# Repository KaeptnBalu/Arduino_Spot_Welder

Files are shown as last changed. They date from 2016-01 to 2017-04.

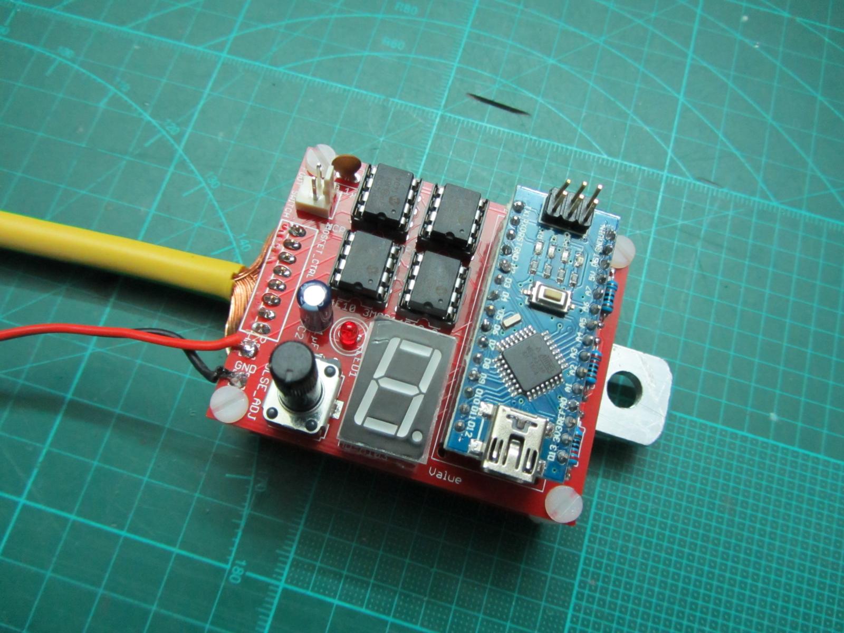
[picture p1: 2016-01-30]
Spot_Welder_Assembly_4.JPG

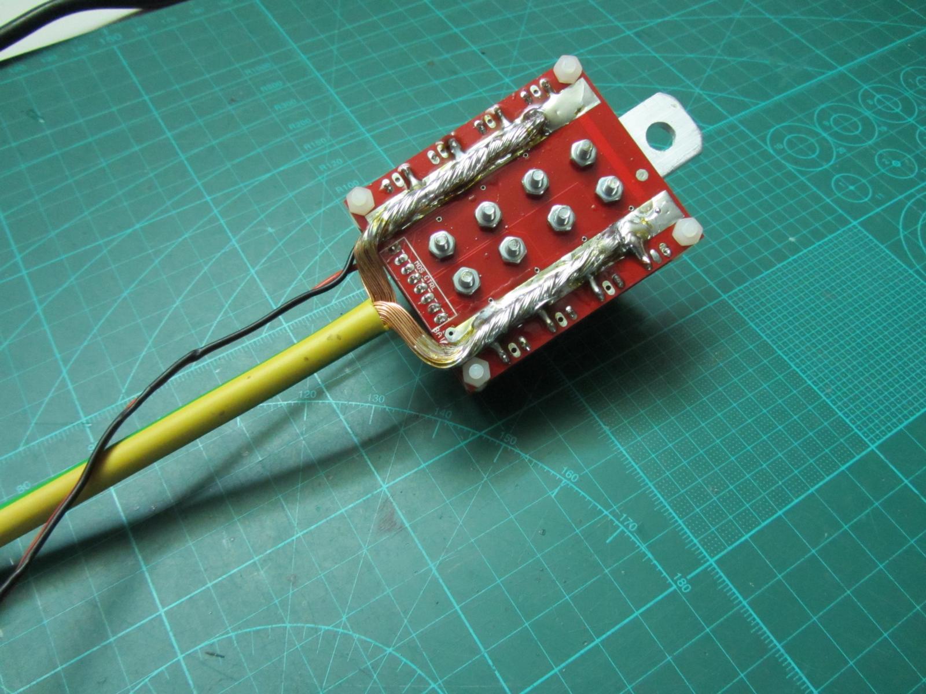
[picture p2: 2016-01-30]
Spot_Welder_Assembly_3.JPG

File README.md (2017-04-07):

# Arduino_Spot_Welder
There is a new Version of this project available: https://github.com/KaeptnBalu/Arduino_Spot_Welder_V2

An Arduino based Spot Welder for battery welding
http://www.instructables.com/id/DIY-Arduino-Battery-Spot-Welder/

This Spot Welder can be used to weld 18650 batteries. It needs a 7-12V power source (12V recommended) and uses a 12V car battery as welding current supply. Typically one 45Ah battery delivers enough current to get good welds with 0.15mm nickel strips. For thicker nickel strips maybe you will need bigger battery or two in paralell.

The Welder generates a double pulse, where the first one is 1/8 of the time of the second one. Pulse time of second pulse is adjustable by the potentiometer and displayed on the screen in mS so you can exactly adjust the time. Its adjustable from 1 ... 20 mS.

If you want to download the project click on "Download ZIP" on this page. Downloading single files sometimes seems to cause some files to be corrupted while downloading.

You can get parts to build your own Spot Welder or prebuilt kits at https://malectrics.eu/

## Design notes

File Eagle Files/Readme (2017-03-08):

The spot welder is made of two boards which are stacked on top of each other.
One board contains all the logic and low power electronic components and the other one contains the Mosfets.

---------------------------------------------------------------------------------------------------------

Update (01.2017): Spot_welder_gerber.zip is now accepted by pcb way without problems

---------------------------------------------------------------------------------------------------------

The gerber files are made to be used at pcbway.com 
You can support me by registering through this link http://www.pcbway.com/setinvite.aspx?inviteid=12824
This way you get a 5$ coupon for your order and i get some credits at the shop which i can use for upcoming projects.

There are two versions of the gerber files available.

1.
You can use the Spot_welder_gerber.zip which has both boards combined to one big board. 
You have to cut this in half at home to get the two single boards.

2.
You can use the Arduino_Board_Gerber.zip and the Mosfet_Board_Gerber.zip . So you have one gerber file for each board. 
This means you have to order both boards seperately which is more expensive, but no cutting at home is required.
(these are not the latest Version at the moment, i will update them in some weeks.)

To download Zip files click on them and then click "view raw". 
Downloading by right click and "save as" does seem to cause problems.

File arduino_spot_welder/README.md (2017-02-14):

The code for the Spot welder is the arduino_spot_welder.ino . Use this for normal operation.

If you built the spot welder yourself but it doesn't work, you can use the TEST_MODE_Arduino_Spot_Welder.ino to find the error.
DO NOT CONNECT THE WELDING WIRES WHEN USING THIS CODE !
With the test code pushing the foot switch turns the mosfets permanent on. This way you can measure all the voltages with a normal multimeter. 
For example you can check: 
- if all mosfet gates get the full voltage when they are on. They should have almost the voltage of your power supply.
- if the Arduino outputs a high signal (5V) to the mosfet drivers
- if the LED gets a high signal (5V)

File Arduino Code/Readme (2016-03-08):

// Simply copy and paste the code into a new sketch in your Arduino Software

int mosfetPin = 5;
int ledPin = 4;
int tasterPin = 2;
int sensorPin = 7;
int sensorValue = 0;
int pulse_time;
int pulse_short;
int pulse_long;

//            0           1          2          3          4          5          6          7          8          9          .
byte z[11]={B11111101, B01100001, B11011011, B11110011, B01100111, B10110111, B10111111, B11100001, B11111111, B11110111, B00000001};

//-------------------------------------------------------------------------------------------

void setup() {

pinMode(tasterPin,INPUT);  // set tasterPin as Input
pinMode(mosfetPin,OUTPUT);  // set mosfetPin as Output
pinMode(ledPin,OUTPUT);  // set ledPin as Output

// 7 Segment Pins
for (int i=6; i <= 13; i++) // 6-13 are set as Outputs
    pinMode(i,OUTPUT);

}

//-------------------------------------------------------------------------------------------

void loop() {

time_display();

// impuls activated by taster
if (digitalRead(tasterPin)==HIGH){
    DoppelImpuls();
    do {
  digitalWrite(mosfetPin, LOW);
  digitalWrite(ledPin, LOW);
} while (digitalRead(tasterPin)==HIGH);
  delay(500);
                                  } 
else 
{
    digitalWrite(mosfetPin, LOW);
    digitalWrite(ledPin, LOW);
}

}

//-------------------------------------------------------------------------------------------

void segmente(byte n) {
// controll all 7 Segments
 
  for(int k=6; k <= 13; k++) {
    if((n & B10000000) > 0)
      digitalWrite(k, HIGH);
    else 
      digitalWrite(k, LOW);
    n = n << 1;
  } 
  }

//-------------------------------------------------------------------------------------------  

void time_display(){  // 7 segment pulse time displaying
  
pulse_time = analogRead(sensorPin)/51.15;

int b=(pulse_time%100)/10;		//Zehner
int a=pulse_time%10;                //Einer

if (b==0)
{
segmente(z[10]);
    delay(100);
}
else
{
segmente(z[b]);
    delay(400);
}    
segmente(z[a]);
    delay(400);
segmente(z[10]);
    delay(700);    
  }

//-------------------------------------------------------------------------------------------

void DoppelImpuls(){  
  sensorValue = analogRead(sensorPin);
 
  pulse_long  = (sensorValue/51.15);   //makes a pulse of max 20 mS because SensorValue can max become 1023
  pulse_short = (pulse_long/8);     // Impuls with 1/8 of the time of pulse_long
 
  if (pulse_short < 1)
     pulse_short = 1; 
 
  digitalWrite(ledPin, HIGH);
  digitalWrite(mosfetPin, HIGH);
  delay(pulse_short);
  digitalWrite(mosfetPin, LOW);
  delay(pulse_short);      
    digitalWrite(mosfetPin, HIGH);
  delay(pulse_long);   
  digitalWrite(mosfetPin, LOW);
  delay(sensorValue);
  digitalWrite(ledPin, LOW);
  
}

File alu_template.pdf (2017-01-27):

17,00 mm

70,00 mm

# Cut from 3 - 4 mm thick aluminum

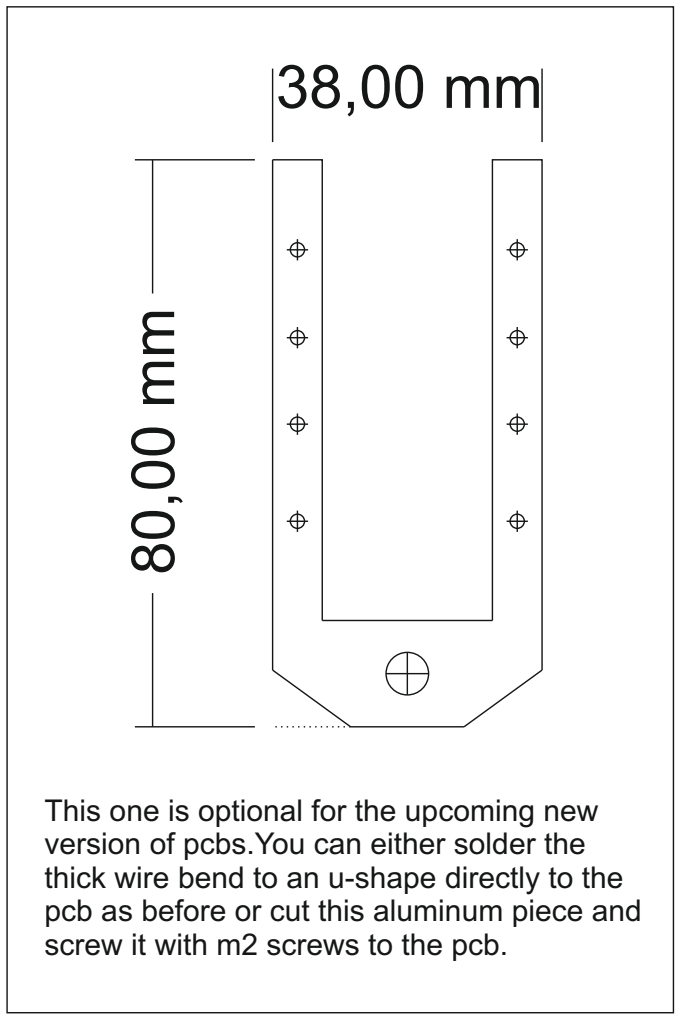
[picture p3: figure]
screw it with m2 screws to the pcb.

This one is optional for the upcoming new version of pcbs.You can either solder the thick wire bend to an u-shape directly to the pcb as before or cut this aluminum piece and

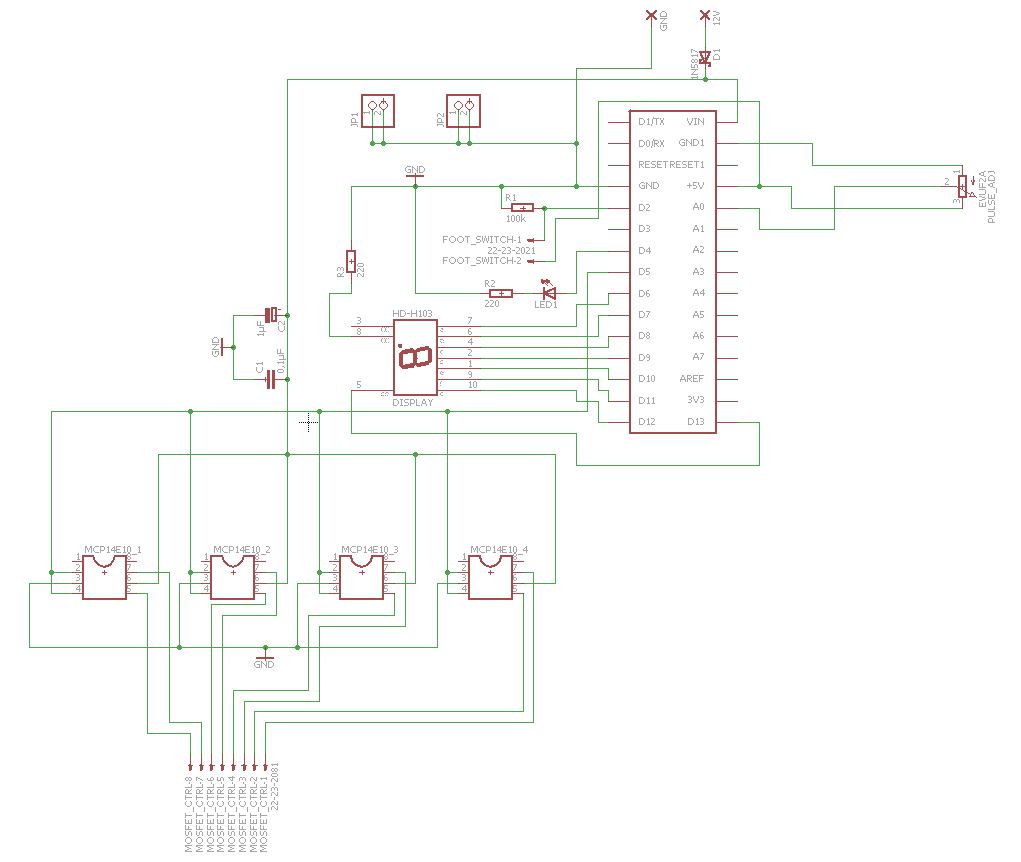
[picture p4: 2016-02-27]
Eagle Files/Arduino_pcb_schematic.JPG

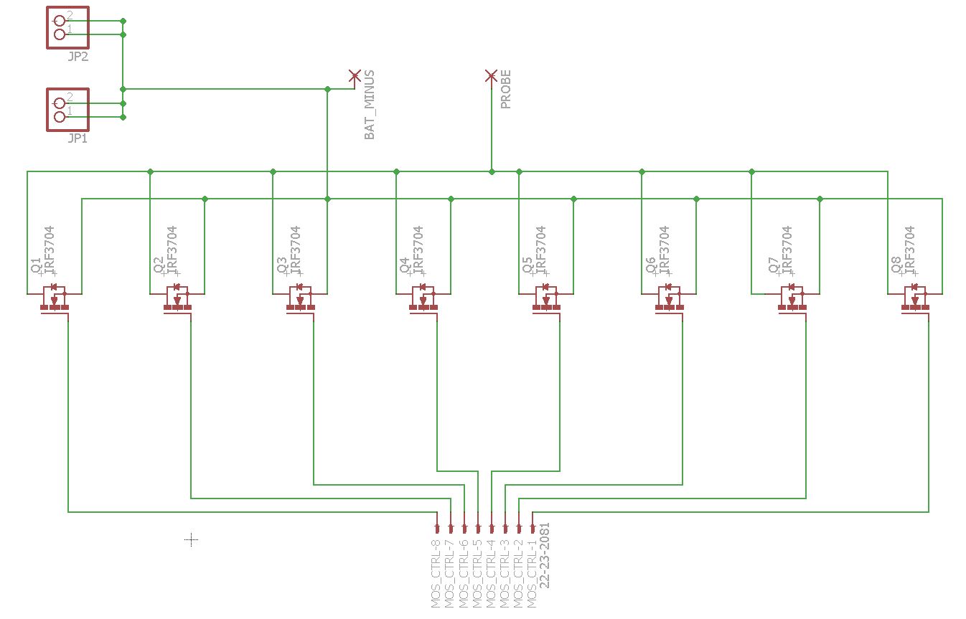
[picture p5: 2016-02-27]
Eagle Files/Mosfet.PCB_schematic.JPG

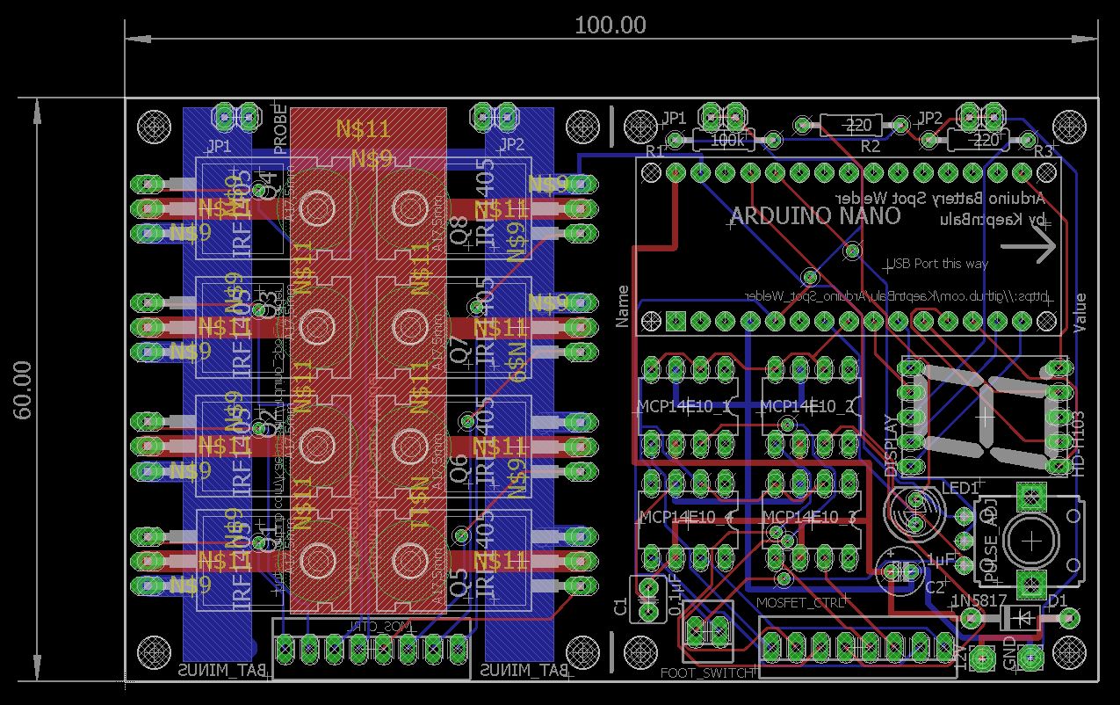
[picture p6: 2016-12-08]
Eagle Files/Gerber_combined_Boards.JPG

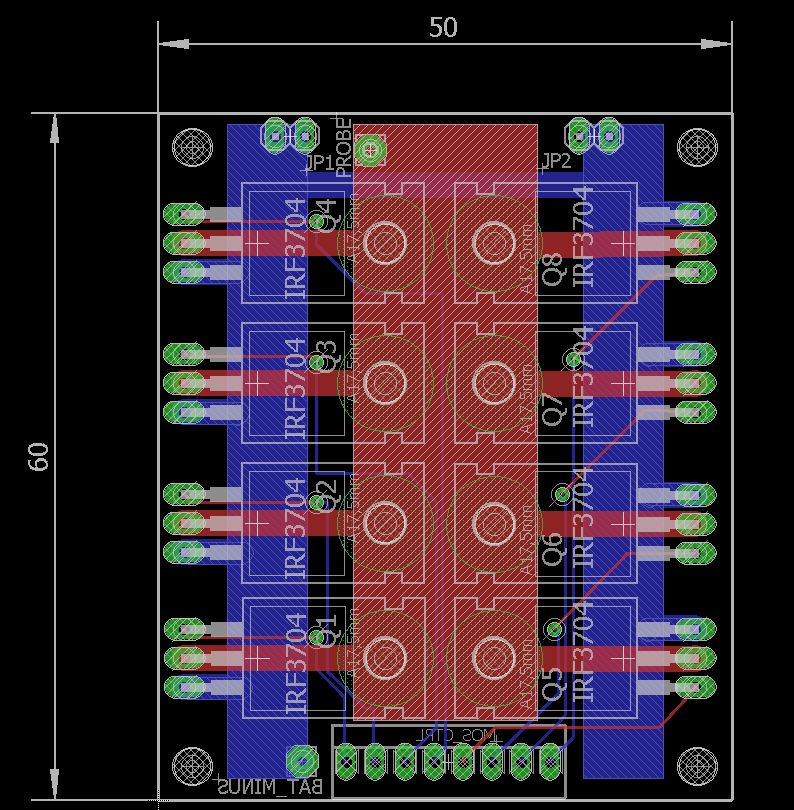
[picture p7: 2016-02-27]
Eagle Files/Mosfet.PCB_board.JPG

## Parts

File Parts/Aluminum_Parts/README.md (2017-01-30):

Use the PDF template to cut the aluminum pieces from 3-4mm material.

The u-shaped piece is optional.
You can either solder the thick wire bend to an u-shape directly to the  pcb as before 
or cut this aluminum piece and screw it with m2 screws to the pcb.
I have not tested the u-shaped alu piece yet because it is quite difficult to manufacture it with hand tools.

You can also take a look at the 3d and dxf drawings to manufacture the aluminum parts with a cnc or something else.

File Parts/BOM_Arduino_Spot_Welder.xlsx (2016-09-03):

 |  | Reichelt.de Parts |  |  | Complete Shopping Card Link (https://secure.reichelt.de/index.html?&ACTION=20&AWKID=1168721&PROVID=2084)
Quantity | Name | Reichelt.de Part Number | Price/piece | Price all | Reichelt.de Link
8 | Mosfet IRF1405 55V 169A | IRF 1405 | 1.15 € | 9.20 € | https://www.reichelt.de/IRC-IRF-Transistoren/IRF-1405/3/index.html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
4 | Mosfet Driver MCP14E10-E/P | MCP 14E10-E/P | 1.70 € | 6.80 € | https://www.reichelt.de/ICs-MCP-1-2-/MCP-14E10-E-P/3/index.html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
1 | Poti 6mm Linear 50K | RK09K113-LIN50K |  | 0.99 € | https://www.reichelt.de/6mm-Potis-mono/RK09K113-LIN50K/3/index.html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
1 | 7 Segment Display | SC 56-11 RT |  | 0.84 € | https://www.reichelt.de/Siebensegment-Anzeigen/SC-56-11-RT/3/index.html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
3 | 1x20pol female header | BL 1X20G8 2,54 | 0.26 € | 0.78 € | https://www.reichelt.de/Buchsenleisten/BL-1X20G8-2-54/3/index.html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
1 | 1x36pol male header | SL 1X36G 2,54 |  | 0.17 € | https://www.reichelt.de/Stiftleisten/SL-1X36G-2-54/3/index.html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
1 | PCB connector set 2pin | PS 25/2G WS |  | 0.29 € | https://www.reichelt.de/Platinen-Steckverbinder/PS-25-2G-WS/3/index.html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
4 | IC socket 8 pole | GS 8 | 0.03 € | 0.12 € | https://www.reichelt.de/IC-Sockel/GS-8/3/index.html?ACTION=3&GROUPID=3215&ARTICLE=8230&START=0&OFFSET=1000
1 | diode 1N5817 | 1N 5817 |  | 0.06 € | https://www.reichelt.de/1N-UF-AA-Dioden/1N-5817/3/index.html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
1 | elektrolytic capacitor 1 µF | RAD 1/63 |  | 0.04 € | https://www.reichelt.de/Elkos-radial-85-C/RAD-1-63/3/index.html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
1 | ceramic capacitor 100pF | KERKO 100P |  | 0.06 € | https://www.reichelt.de/Scheiben/KERKO-100P/3/index.html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
2 | Resistor 221 Ohm | METALL 221 | 0.08 € | 0.16 € | https://www.reichelt.de/1-4W-1-100-Ohm-976-Ohm/METALL-221/3/index.html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
1 | Resistor 100K-Ohm | METALL 100K |  | 0.08 € | https://www.reichelt.de/1-4W-1-100-k-Ohm-976-k-Ohm/METALL-100K/3/index.html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
1 | LED 5mm green | LED 5MM GN |  | 0.06 € | https://www.reichelt.de/LEDs-5-mm/LED-5MM-GN/3/index.html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
 |  | Other Parts
1 | Arduino Nano |  |  | 1.70 € | Aliexpress.com
1 | Aluminium 16x70x5mm |  |  | 2 € | local hardware Store
1 | 2m thick cable 16 or 25 mm² |  |  | 0 € | e.g. old car starter cable
1 | 0,5m 10mm² solid copper wire | for the welding tips |  | 1 € | local hardware store
3 | cable lug for 16 - 25mm² |  | 0.6 | 1.80 € | local hardware store or http://www.voelkner.de/products/9287/Ringkabelschuh-16-25mm-6mm-Gelb.html
1 | battery clip | for car battery |  | 1.95 € | local hardware store or http://www.voelkner.de/products/80594/Batterieklemme-Gerade-Plus-Minus.html
1 | PCB | from pcb manufacturer |  | 20.00 € | pcbway.com (you get 10 pcbs for this price)
 |  | TOTAL PARTS COST |  | 48.10 €

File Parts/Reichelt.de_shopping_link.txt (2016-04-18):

https://secure.reichelt.de/index.html?&ACTION=20&AWKID=1203408&PROVID=2084

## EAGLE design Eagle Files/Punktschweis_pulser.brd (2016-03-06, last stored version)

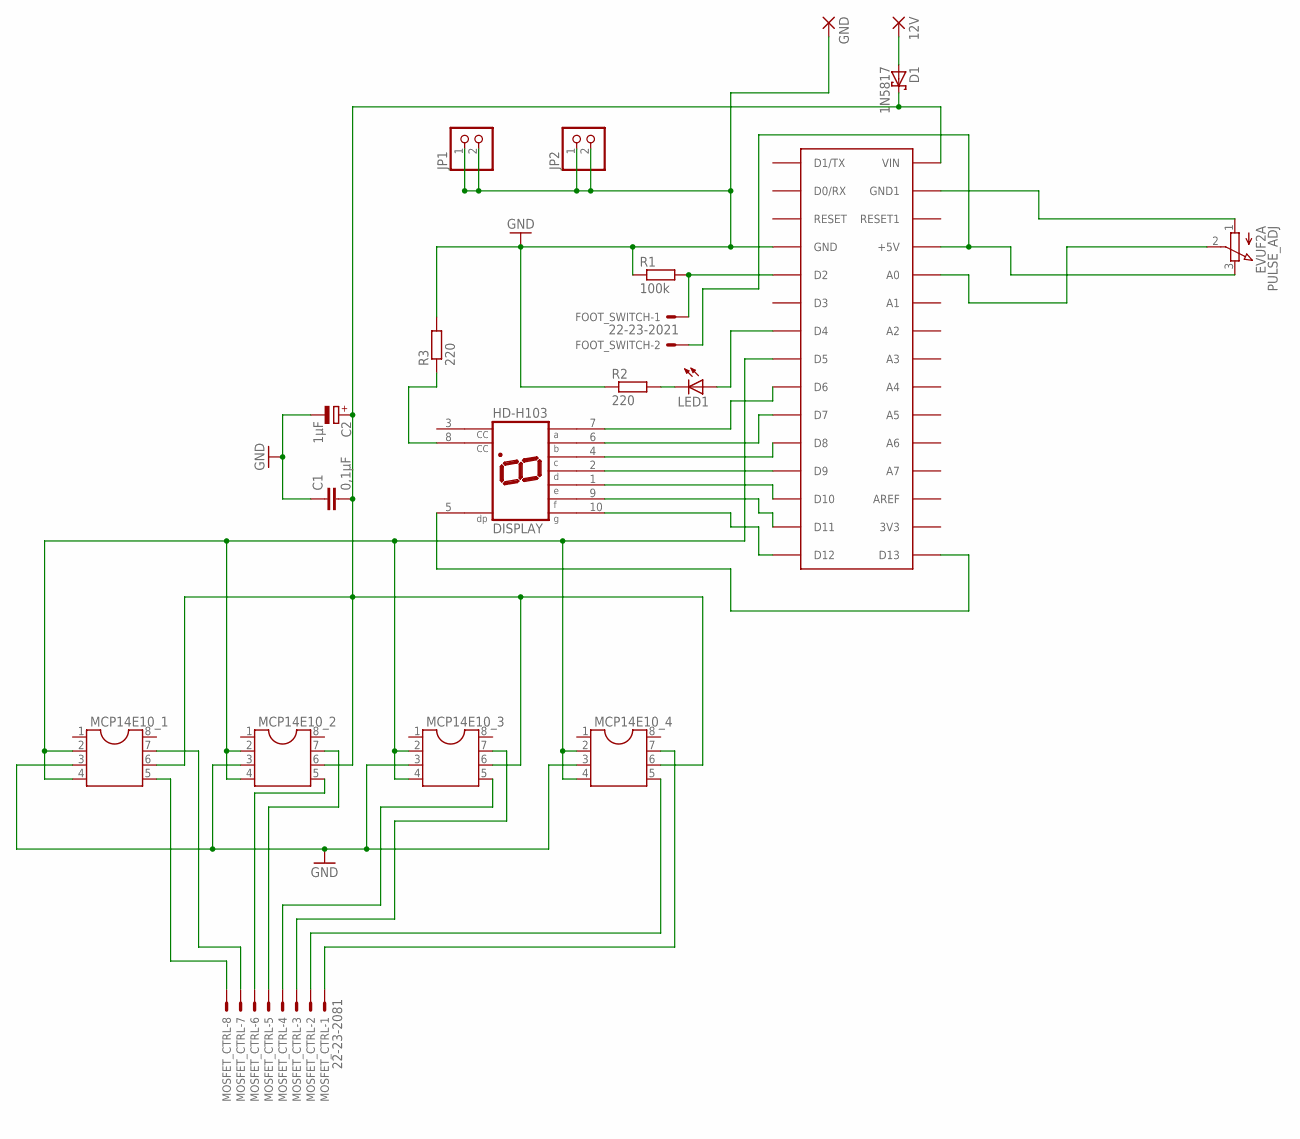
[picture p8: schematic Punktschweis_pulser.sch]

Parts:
12V: 2,54/0,8
C1: 0,1µF; C2.5-4
C2: 1µF; E2-5
D1: 1N5817; DO41-10
DISPLAY: HD-H103; HDSP-M
FOOT_SWITCH: 22-23-2021
GND: 2,54/0,8
JP1, JP2: PINHD-1X2; 1X02
LED1: LED5MM
MCP14E10_1, MCP14E10_2, MCP14E10_3, MCP14E10_4: DIL8; DIL08
MOSFET_CTRL: 22-23-2081
PULSE_ADJ: EVUF2A; EVUF
R1: 100k; 0207/10
R2, R3: 220; 0207/10
U$1: ARDUINONANO; PDIP-32

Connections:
GND: C1.1, C2.-, GND.1, JP1.1, JP1.2, JP2.1, JP2.2, MCP14E10_1.3, MCP14E10_2.3, MCP14E10_3.3, MCP14E10_4.3, R1.1, R2.1, R3.2, U$1.GND
unnamed: DISPLAY.7 (A), U$1.D6
unnamed: MCP14E10_1.5, MOSFET_CTRL.8
unnamed: C1.2, C2.+, D1.C, MCP14E10_1.6, MCP14E10_2.6, MCP14E10_3.6, MCP14E10_4.6, U$1.VIN
unnamed: PULSE_ADJ.1 (A), U$1.GND1
unnamed: FOOT_SWITCH.2, PULSE_ADJ.3 (E), U$1.+5V
unnamed: PULSE_ADJ.2 (S), U$1.A0
unnamed: FOOT_SWITCH.1, R1.2, U$1.D2
unnamed: LED1.K (C), R2.2
unnamed: LED1.A, U$1.D4
unnamed: MCP14E10_1.7, MOSFET_CTRL.7
unnamed: MCP14E10_2.5, MOSFET_CTRL.6
unnamed: MCP14E10_2.7, MOSFET_CTRL.5
unnamed: DISPLAY.6 (B), U$1.D7
unnamed: MCP14E10_3.5, MOSFET_CTRL.4
unnamed: MCP14E10_3.7, MOSFET_CTRL.3
unnamed: MCP14E10_4.5, MOSFET_CTRL.2
unnamed: MCP14E10_4.7, MOSFET_CTRL.1
unnamed: DISPLAY.4 (C), U$1.D8
unnamed: MCP14E10_1.2, MCP14E10_1.4, MCP14E10_2.2, MCP14E10_2.4, MCP14E10_3.2, MCP14E10_3.4, MCP14E10_4.2, MCP14E10_4.4, U$1.D5
unnamed: DISPLAY.2 (D), U$1.D9
unnamed: DISPLAY.1 (E), U$1.D10
unnamed: DISPLAY.9 (F), U$1.D11
unnamed: DISPLAY.10 (G), U$1.D12
unnamed: DISPLAY.5 (DP), U$1.D13
unnamed: DISPLAY.8 (CC), R3.1
unnamed: 12V.1, D1.A

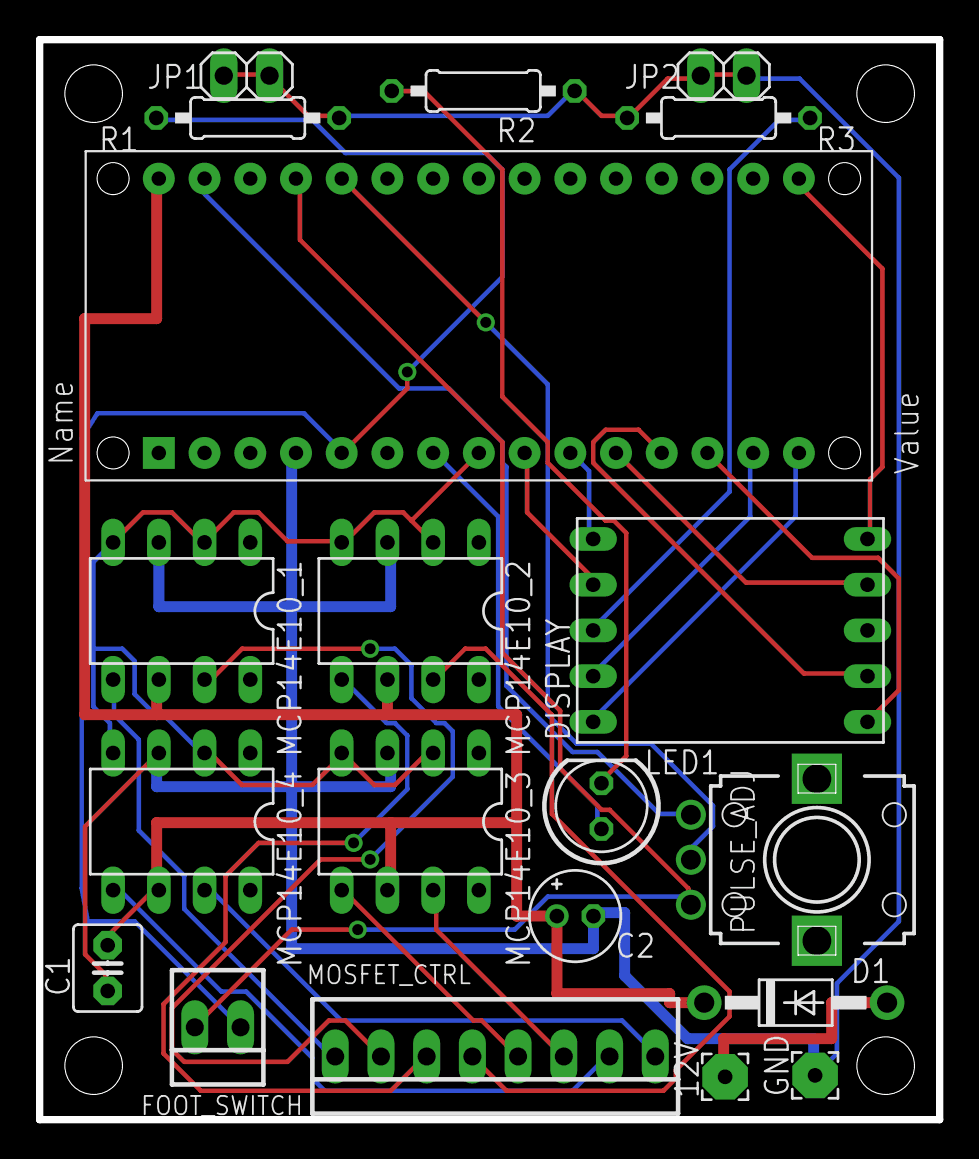
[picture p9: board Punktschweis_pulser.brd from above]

Board: 2 copper layers, 50.0 x 60.0 mm, 20 parts (0 on the bottom side), 27 nets.

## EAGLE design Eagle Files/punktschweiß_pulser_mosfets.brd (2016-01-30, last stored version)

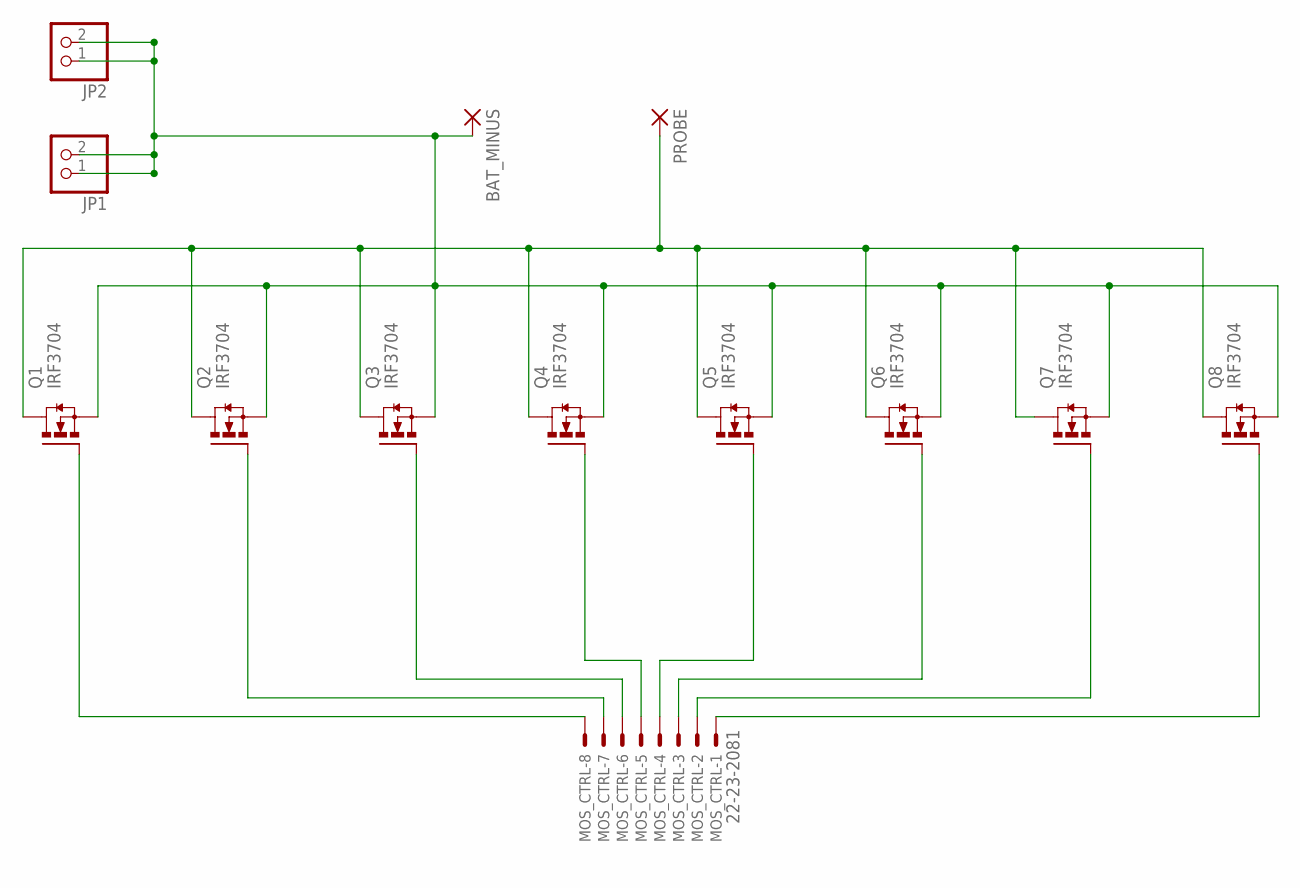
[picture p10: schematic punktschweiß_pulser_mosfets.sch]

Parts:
BAT_MINUS: 2,54/0,9
JP1, JP2: PINHD-1X2; 1X02
MOS_CTRL: 22-23-2081
PROBE: 2,54/0,9
Q1, Q2, Q3, Q4, Q5, Q6, Q7, Q8: IRF3704; TO220AH

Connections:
unnamed: MOS_CTRL.8, Q1.B (G)
unnamed: MOS_CTRL.7, Q2.B (G)
unnamed: MOS_CTRL.6, Q3.B (G)
unnamed: MOS_CTRL.5, Q4.B (G)
unnamed: MOS_CTRL.4, Q5.B (G)
unnamed: MOS_CTRL.3, Q6.B (G)
unnamed: MOS_CTRL.2, Q7.B (G)
unnamed: MOS_CTRL.1, Q8.B (G)
unnamed: BAT_MINUS.1, JP1.1, JP1.2, JP2.1, JP2.2, Q1.E (S), Q2.E (S), Q3.E (S), Q4.E (S), Q5.E (S), Q6.E (S), Q7.E (S), Q8.E (S)
unnamed: PROBE.1, Q1.C (D), Q2.C (D), Q3.C (D), Q4.C (D), Q5.C (D), Q6.C (D), Q7.C (D), Q8.C (D)

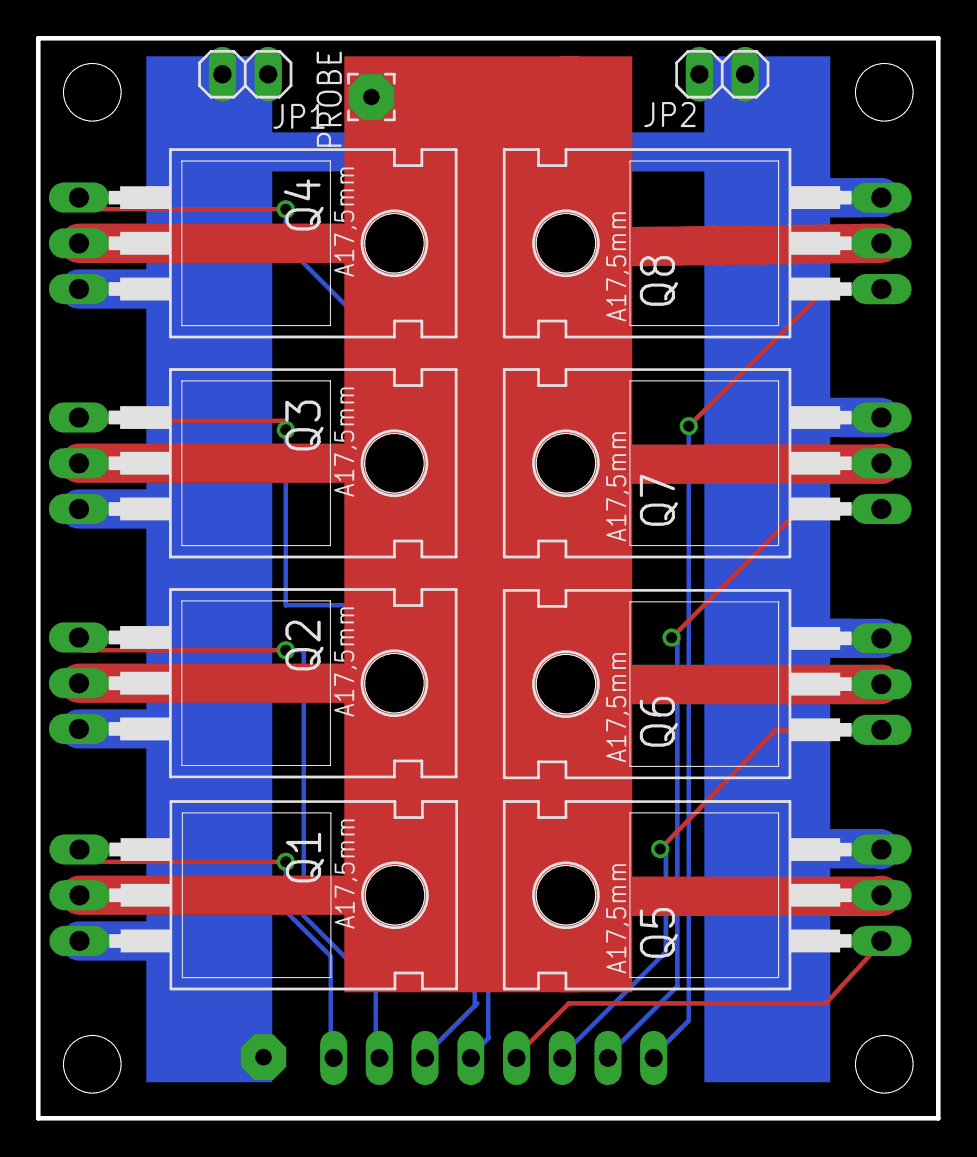
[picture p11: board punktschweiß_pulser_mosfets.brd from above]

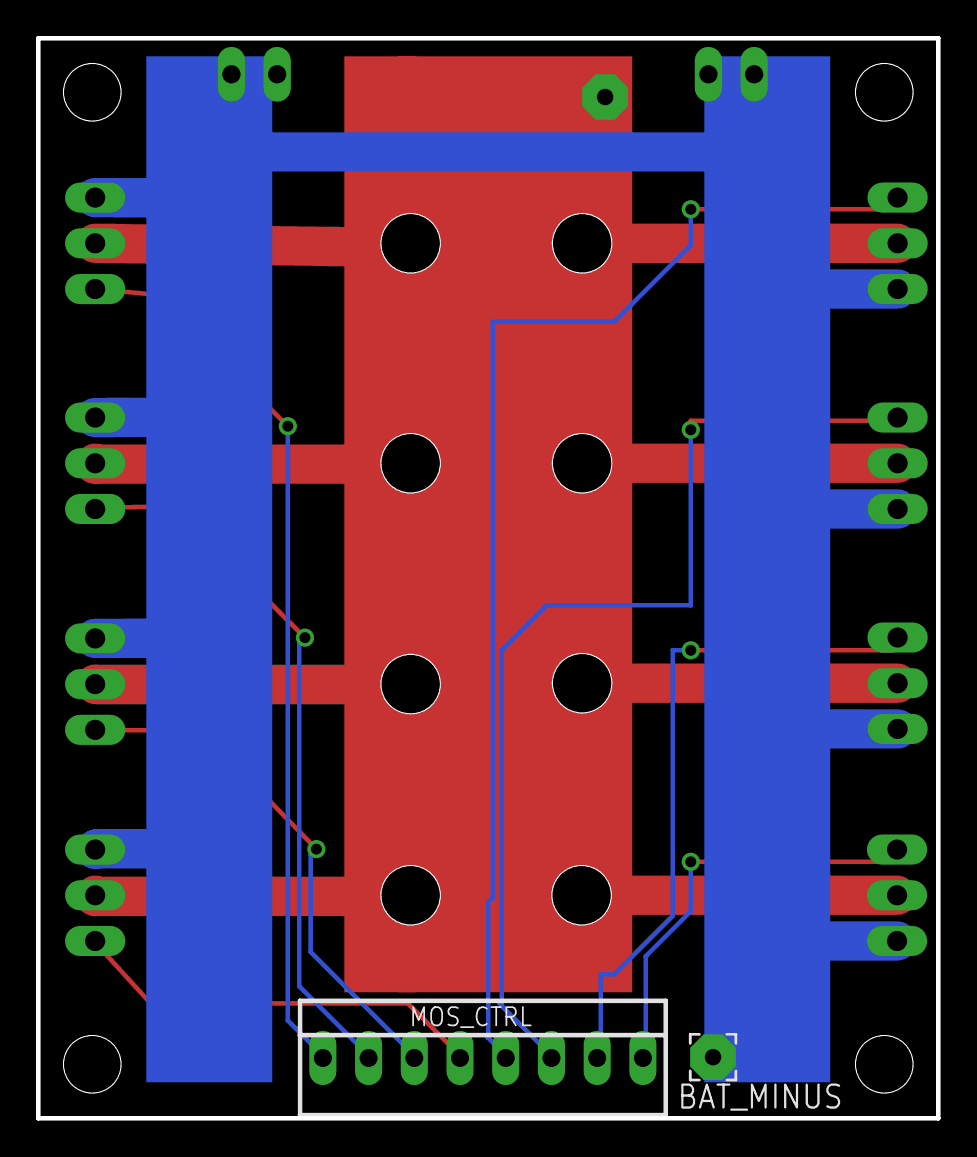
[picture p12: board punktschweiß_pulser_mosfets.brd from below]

Board: 2 copper layers, 50.0 x 60.0 mm, 13 parts (2 on the bottom side), 10 nets.

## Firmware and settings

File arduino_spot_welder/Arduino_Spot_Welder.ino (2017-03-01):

// Arduino Battery Spot Welder
// Project Page: http://www.instructables.com/id/DIY-Arduino-Battery-Spot-Welder/

int max_pulse_time = 20; // Sets the maximum pulse time to 20mS (do not use higher than 99 because the display only works up to 99)
int mosfetPin = 5;  // Pin that controls the mosfet drivers
int ledPin = 4;   // Pin to control the status led
int switchPin = 2;  // Pin to trigger a pulse with the foot switch
int sensorPin = A7;  // Pin where the potentiometer value is read
int previous_pulse_time; // Previous pulse time so display can skip to ones digit
int pulse_time;   // Variable to store the pulse time
int pulse_short;  // Variable to store the short pulse time
int displayStep = 0; // The step the display function should complete next
unsigned long previousMillis = millis(); // The milliseconds where the timer starts counting from
int tens = 0; // Tens place digit
int ones = 0; // Ones place digit
float pulse_calc = 1023 / max_pulse_time;

// Defines the possible characters to be displayed on the 7-segment display in an array
//            0          1          2          3          4          5          6          7          8          9          .          None       All
byte y[13] = {B11111100, B01100000, B11011010, B11110010, B01100110, B10110110, B10111110, B11100000, B11111110, B11110110, B00000001, B00000000, B11111111}; // Ones
byte z[13] = {B11111100, B00001100, B11011010, B11110010, B01100110, B10110110, B10111110, B11100000, B11111110, B11110110, B00000001, B00000000, B11111111}; // Tens


//-------------------------------------------------------------------------------------------

void setup() {
  pinMode(switchPin, INPUT); // Set switchPin as Input
  pinMode(mosfetPin, OUTPUT); // Set mosfetPin as Output
  pinMode(ledPin, OUTPUT); // Set ledPin as Output
  pinMode(sensorPin, INPUT); // Set sensorPin as Input

  // Set up 7 Segment Pins
  for (int i = 6; i <= 13; i++) // Pins 6-13 are set as Outputs
    pinMode(i, OUTPUT);

  // Light up the led and the display 2 seconds to verify correct placement and function
  digitalWrite(ledPin, HIGH);
  segments(z[12]);
  delay(2000);
  digitalWrite(ledPin, LOW);
  segments(z[11]);
}

//-------------------------------------------------------------------------------------------

void loop() {

  // Read pulse time from analog input
  read_pulse_time();

  // Display time on 7-segment display
  time_display();

  // Impulse activated by switch
  if (digitalRead(switchPin) == HIGH && pulse_time > 0) {
    double_pulse();
    // Wait until switch has been released
    do {
      digitalWrite(mosfetPin, LOW);
      digitalWrite(ledPin, LOW);
    } while (digitalRead(switchPin) == HIGH);
    // Delay before impulse can be triggered again
    delay(500);
  }
  else
  {
    digitalWrite(mosfetPin, LOW);
    digitalWrite(ledPin, LOW);
  }
}

//-------------------------------------------------------------------------------------------

void segments(byte n) {
  // controll all 7 Segments

  for (int k = 6; k <= 13; k++) {
    if ((n & B10000000) > 0)
      digitalWrite(k, HIGH);
    else
      digitalWrite(k, LOW);
    n = n << 1;
  }
}

//-------------------------------------------------------------------------------------------

void read_pulse_time() {
  // Read the potentiometer and shift the value to correct the midpoint
  // This allows 20 to be selected without the value having to be exactly 1023
  int sensorValue = analogRead(sensorPin) + pulse_calc/2;

  // Add a small amount of hysteresis
  if ((sensorValue - 3) / pulse_calc > pulse_time) {
    // Makes a pulse of max 20 mS because SensorValue can max become 1023
    pulse_time = sensorValue / pulse_calc;
  }
  if ((sensorValue + 3) / pulse_calc < pulse_time) {
    pulse_time = sensorValue / pulse_calc;
  }
}

//-------------------------------------------------------------------------------------------

void reset_timer() {
  // Set timer to start counting from current time
  previousMillis = millis();
}

//-------------------------------------------------------------------------------------------

bool delay_done(unsigned long delay) {
  // If difference between current time and previous time is more than the delay
  if ((unsigned long)(millis() - previousMillis) >= delay) {
    return true;
  }
  return false;
}

//-------------------------------------------------------------------------------------------

void time_display() { // 7 segment pulse time displaying
  if (pulse_time != previous_pulse_time) {
    previous_pulse_time = pulse_time;

    // Skip to ones digit
    displayStep = 2;
  }

  if (tens == 0) {
    // Skip to ones digit
    displayStep = 2;
  }

  tens = (pulse_time % 100) / 10; // Tens place
  ones = pulse_time % 10; // Ones place

  //delay(500);

  switch (displayStep) {
    // Display tens digit
    case 0:
      // Time to clear display after displaying both digits
      if (delay_done(400)) {
        // Display tens digit
        segments(z[tens]);

        reset_timer();
        displayStep = 1;
      }
      break;

    // Delay after showing tens digit
    case 1:
      if (delay_done(300)) {
        // Clear display
        segments(z[11]);

        displayStep = 2;
      }
      break;

    // Display ones digit
    case 2:
      segments(y[ones]);

      reset_timer();
      displayStep = 3;

      break;

    // Delay after showing ones digit
    case 3:
      if (delay_done(300)) {
        // Clear display
        segments(z[11]);

        reset_timer();
        displayStep = 0;
      }
      break;
  }
}

//-------------------------------------------------------------------------------------------

void double_pulse() {

  pulse_short = (pulse_time / 8); // Impulse with 1/8 the time of pulse_time

  if (pulse_short < 1) // Makes the short pulse at least one millisecond
    pulse_short = 1;

  digitalWrite(ledPin, HIGH);
  digitalWrite(mosfetPin, HIGH);
  delay(pulse_short);
  digitalWrite(mosfetPin, LOW);
  delay(pulse_short);
  digitalWrite(mosfetPin, HIGH);
  delay(pulse_time);
  digitalWrite(mosfetPin, LOW);

  // Keep LED on for extra 50ms
  delay(50);
  digitalWrite(ledPin, LOW);

}

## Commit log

2016-01-30 Create Arduino Nano Code
2016-01-30 Arduino Nano Code
    the code run the spot welder
2016-01-30 Eagle files of the two boards
    [Punktschweis_pulser.brd, Punktschweis_pulser.sch, punktschweiß_pulser_mosfets.brd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]
2016-01-30 assembly pictures
2016-01-30 parts to buy
    [Reichelt__Shopping_List.csv]
2016-02-01 BOM update
    [BOM_Arduino_Spot_Welder.xlsx, Reichelt__Shopping_List.csv]
2016-02-27 added pcb board to the BOM
    [BOM_Arduino_Spot_Welder.xlsx]
2016-02-27 Arduino Code Readme
2016-02-27 added schematic and board pictures
2016-03-06 Added Gerber Files for pcbway.com
    [Punktschweis_pulser.brd]
2016-03-08 Gerber files description
2016-03-09 Make it Arduino friendly. just double click the .ino
2016-03-09 Add project desc, first test case
2016-03-09 fixed led
2016-03-17 Image of the Gerber File Board Layout
2016-04-02 gerber board outlines fixed
2016-04-18 BOM updated
    [BOM_Arduino_Spot_Welder.xlsx]
2016-05-10 Single boards gerber added
2016-06-12 Gerber improved
2016-06-13 removed dashed line from gerber
2016-09-03 Update Arduino sketch
    I have made lots of changes, but none to the features or operation of the spot welder. Mainly I have improved the display subroutine and the potentiometer reading.
    Most important changes:
    - Display code is now non-blocking. So pulse will happen as soon as switch is pressed, not a few hundred milliseconds later
    - Display updates immediately and shows ones place digit when adjusting pot
    - "1" digit in tens place shows on left which is more readable
    - Hysteresis added to the potentiometer reading
    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
2016-09-03 Update Reichelt Part List
    [BOM_Arduino_Spot_Welder.xlsx]
2016-12-08 Add files via upload
    little fixes on the silkscreen layer
2017-01-27 Add files via upload
    Some small improvements to the pcb layout
2017-02-14 Code to find failures in the circuit
    [TEST_MODE_Arduino_Spot_Welder.ino]
2017-02-14 Arduino Code Instructions
